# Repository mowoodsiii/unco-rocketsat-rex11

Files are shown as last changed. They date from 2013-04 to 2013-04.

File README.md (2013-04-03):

unco-template
==============
This is the official git repository for the UNCo template project. 

Source (html) for the project's web page is stored in the gh-pages branch of this project. The site is hosted by github, and may be viewed here: [Heliostat Project Page](http://pack3754.github.com/unco-template/index.html)

You may also be interested in the main UNCo Physics Students: Research and Resources pages: [UNCo Physics Students: Research and Resources](http://pack3754.github.com/unco-physics-research)

# project files:
The files are organized into the following structure:
* CMakeLists.txt - cross platform makefiles to make compiling the Heliostat package for any platform (linux, Windows and Mac) easy!
* config - top-level package configuration, including versionn numbers and doxygen configuration files.
* docs - All project documentation will be organized here.
* docs/doxy - Additional doxygen pages to help with source code documentation 
* docs/exported - published (pdf) versions of any important documents
* docs/images - images for use in papers, the web, and documentation
* hw - hardware design documents
* include - distribution header files for the Heliostat C/C++ API

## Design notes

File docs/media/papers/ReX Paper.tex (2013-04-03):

\documentclass{article}
\usepackage{graphicx}
\usepackage{color}
\usepackage{mathptmx}
\usepackage{gensymb}
\usepackage{amsmath}
\usepackage{float}
\usepackage{setspace}
\usepackage[top=1in, bottom=1in, left=1in, right=1in]{geometry}
\usepackage{fancyhdr}
\newcommand{\HRule}{\rule{\linewidth}{0.5mm}}
\setlength{\headheight}{15.2pt}
\pagestyle{fancy}

%\pagestyle{myheadings}
\lhead{\bfseries Reentry Experiment SAT-X}
\chead{\textbf{} U. Northern Colorado}
\rhead{\em \today}

\begin{document}
%%%TITLE PAGE%%%
	\begin{titlepage}
		\begin{center}
			% Upper part of the page
			\textsc{\LARGE Un\underline{iversity of Northern Colora}do}\\[0.7cm]
			\textsc{\Large Colorado Space Grant Symposium}\\[0.7cm]
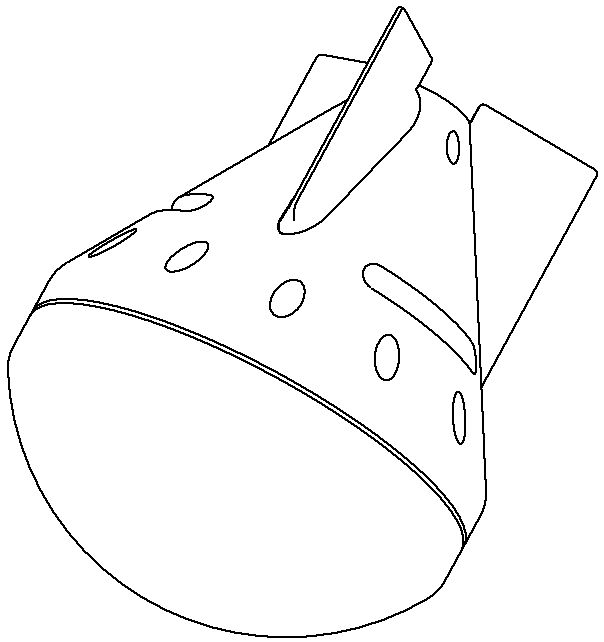
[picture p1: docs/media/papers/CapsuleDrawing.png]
			\\[1cm]
			% Title
			\HRule \\[0.4cm]
			{ \huge \bfseries Reentry Experiment SAT-X:\\} \large Developing an Optimal Atmospheric Reentry Vehicle for the Rocket SAT-X Program\\[0.4cm]
			\HRule \\[1.3cm]
			% Author and supervisor
				\begin{minipage}{0.4\textwidth}
					\begin{flushleft} \large
						\emph{Authors:}\\
						Aaron \textsc{Adamson}\\
						Jordan \textsc{Aken}\\
						Motoaki \textsc{Honda}\\
						Casey \textsc{Kuhns}\\
						Rob \textsc{Shiely}\\
						Maurice \textsc{Woods} (PM)
					\end{flushleft}
				\end{minipage}
				\begin{minipage}{0.4\textwidth}
					\begin{flushright} \large
						\emph{Advisors:} \\
						Cynthia \textsc{Galovich}\\
						Matthew \textsc{Semak}\\
						Robert \textsc{Walch}\\
					\end{flushright}
				\end{minipage}
				\vfill
				\vspace{.75cm}
			% Bottom of the page
				\begin{minipage}{0.4\textwidth}
					\begin{flushleft} 
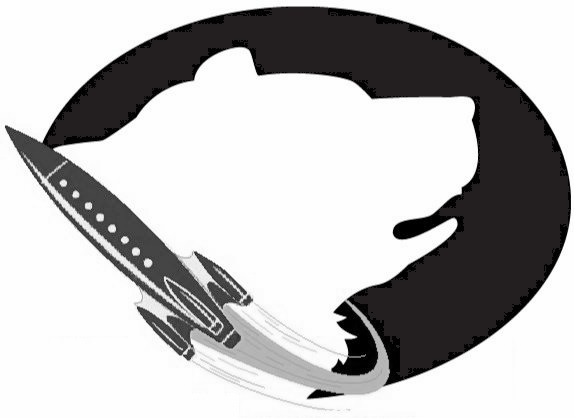
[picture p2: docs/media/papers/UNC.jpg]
						\\
					\end{flushleft}
				\end{minipage}
				\begin{minipage}{0.4\textwidth}
					\begin{flushright}
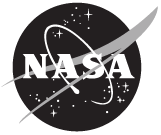
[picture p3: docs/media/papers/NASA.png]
						\\
					\end{flushright}
				\end{minipage}

			{\large \today}\\
			Revision 2
		\end{center}
	\end{titlepage}

%%%BEGIN DOCUMENT%%%
\newpage
%Table of Contents
\tableofcontents	
\newpage

%Abstract
\section{Abstract}
	\begin{doublespace}
	\indent\indent The Reentry Experiment SAT-X (ReX), a joint venture between University of Northern Colorado (UNC) Physics and the Colorado Space Grant Consortium (COSGC), was designed to identify key design aspects associated with atmospheric reentry vehicles and to provide test data that will help to remove dependency on over-engineering as a primary engineering strategy. One of the important considerations for space exploration involves the structural challenges experienced by spacecraft upon returning to Earth. The challenge of entering, or reentering, the Earth's atmosphere is not new, and for years NASA has successfully designed vessels that have endured the harsh process of reentry. However, surprisingly little is actually known about the high atmosphere of Earth. With the insight gained from a simple model of a reentry vehicle's interaction with the atmosphere, a variety of prototypes were tested to determine which design stood the best chance of achieving the ReX mission goals. The ReX payload was launched from Wallops Island at NASA's Wallops Flight Facility in Virginia on 21 July 2011. Funded by the COSGC as part of the Rocket SAT-X undergraduate research program, the payload was flown on an Improved Terrier Orion sounding rocket, and it successfully deployed a small aluminum capsule at apogee (at an altitude of approximately 120 km). The flight was intended to function as a means for characterizing the reentry process and as a proof-of-concept test, showing that the capsule design was an effective platform that could be used for further atmospheric research in the Rocket SAT-X program. The payload design was effective at ejecting a vessel from a spacecraft with few moving parts; it can be constructed in less than a month with less than a \$3000 budget, and it is easily modifiable to accommodate new mission hardware (ideal for the Rocket SAT-X program). We are currently revising the ReX design in an attempt to improve the payload's radio telemetry connection, thus increasing the amount of data recovered from the flight and improving the resolution and dependability of the payload's instruments.
	\end{doublespace}

%Introduction
\section{Introduction}
	\begin{doublespace}
		\indent\indent The challenge of entering, or reentering, the Earth's atmosphere is not new. For years, NASA has successfully designed vessels that have endured the harsh process of reentry. However, in some cases, this was made possible through the act of over-engineering; designing to withstand conditions far beyond what is expected to be encountered. Though this method has proven effective, consider the benefit of knowing exactly what to expect. The objective of the University of Northern Colorado Reentry Experiment SAT-X (UNC ReX) was to shed light on the process of atmospheric reentry and provide test data that will help to remove our dependency on over-engineering. Moreover, as a secondary objective, the capsule's design was evaluated to determine its effectiveness in serving as a platform for use in future Rocket SAT-X missions. This evaluation took into account the resources and skills needed to produce the capsule.\\
		\indent This mission was carried out as a part of UNC Physics' involvement with ``Rocket SAT-X", an outreach program funded by the Colorado Space Grant Consortium (COSGC) that presents undergraduate students with an opportunity to become involved in aerospace engineering and the aerospace community at an advanced level. The Rocket SAT-X program challenges students to design and fabricate an experimental payload that will be launched on a Terrier-Orion sounding rocket, provided and launched by NASA's Wallops Flight Facility in Virginia. Four university-made payloads were launched approximately 120km into space, where the rocket then shed its fairing, exposing the payloads to the space environment (Figure~\ref{timeline}). \\
		\indent In an effort to document the methods used throughout this project, this report will discuss both the physics and the engineering behind the reentry experiment for future reentry Rocket SAT-X missions.
	%Mission Statement and Background
	\subsection{Mission Statement and Background}
	\begin{center}
		\emph{To provide a robust design of a deployable and recoverable payload for institutions to use on future Rocket SAT-X missions. With the provision of local data storage, we can greatly increase the amount of data recovered by eliminating the need to transmit restricted amounts of data to the ground.}\\
	\end{center}
		\indent\indent  By collecting extensive dynamical and thermal data as the reentry vehicle enters the earth's atmosphere, ReX aims to provide information on the reentry process of a particular type of vehicle. After reviewing the flight data and comparing it to a mathematical model (outlined in the Methods section) the design of the capsule will be reviewed for its effectiveness as a reentry vehicle. Moreover, this data will be used in refining the model to aid in optimizing the payload design. This analysis will be conducted to the extent that any future Rocket SAT-X team using this capsule platform will be able to predict the details of the capsule's motion (its trajectory and motion about its center of mass), what temperatures will be experienced during flight, and what the general limitations of the capsule platform will be at any given time during a mission.
	%Success Criteria
	\subsection{Success Criteria}
		\indent\indent In order to achieve full `missions success', the ReX payload was required to collect enough usable data at a high enough resolution to create a reliable flight characterization profile for the ReX reentry vehicle. Additionally, this had to be achieved while optimizing the vehicle's mass, size and technological complexity -- a secondary objective to the ReX mission. The resolution needed to create such a profile is determined by the ability of the onboard sensors to detect both large and small deviations in the vehicle's flight path, such as oscillations, high-G accelerations, and turbulence. Also, since extreme heat is characteristic of the reentry process, sensors were required to measure where heat builds up on the vehicle surface. Finally, the payload was designed to survive long enough to allow  data collection until impact (splashdown).\\
		\indent ``Full mission success" would only have been claimed if all of these objectives were met. However, considering the possibility that some objectives may not be met for any reason, levels of ``partial mission success" could be achieved if some of the more basic functions of the payload worked correctly despite the failure of other functions (e.g. if the capsule is ejected but data were not transmitted back to the rocket, then the mission would be considered a ``partial mission objective success").\\
		\indent It is important to note that the mission supervisors at Wallops Flight Facility and the COSGC instated a number of mission requirements beyond those set by the ReX team. Given that the ReX payload involved the ejection of a reentry vehicle that was designed to remain intact throughout descent and splashdown, concern was raised about the possibility of the payload landing in a populated area, presenting a potential hazard to those civilians who may be near a debris fallout area. NASA requires that spacecraft reentry must not exceed a 1:10,000 probability of exposing the ground population to risk (Rochelle, 2004). Therefore, the team was required to ensure that the reentry vehicle would be ejected in a manner that would minimize the risk of becoming a hazard to the ground population. An ejection velocity of no more than $5\frac{m}{s}$ was predicted to keep the capsule within a safe impact radius.
		\end{doublespace}
		
%Methods
\section{Methods}
	\begin{doublespace}
	\indent\indent In an effort to better understand the conditions that would be experienced during the reentry process, the ReX team first studied the fundamental physics of the expected descent. Using a mathematical model, the team optimized the payload's design by building the capsule to specifications that were calculated to enable the capsule to survive the descent from apogee and impact with the ocean.
	%Physics of Reentry
	\subsection{Physics of Reentry}
	\indent\indent Using MATLAB (a technical computing environment), Motoaki Honda developed several programs for use in modeling the flight of the capsule. The programs were to serve three purposes: 1) predict the force of impact that the capsule experiences upon splashdown, 2) predict the amount of energy due to air friction that is imparted to the capsule during its descent (calculate the heat of reentry), and 3) provide a graphical user interface testing tool for visualizing the instantaneous orientation of the capsule during drop tests (also used to ``monitor" the motion of the capsule during flight). The following subsections are an overview of some of the basic concepts that were used in the mathematical model.
		%Forces
		\subsubsection{Forces}
		\indent\indent To model the process of atmospheric reentry, it is important to know what forces are being exerted on the reentry vehicle. Taking a purely Newtonian approach, the most prominent force  associated with reentry is air resistance (Pardini and Anselmo, 2004). This is expressed by
		\begin{equation}
			F_{air drag}=\frac{1}{2}\rho(h) v^{2}AC_{d},
		\end{equation}
		where $\rho$(h) is air density as a function of the altitude, h, above the surface of the earth, $v$ is the capsule's speed, A is the capsule's cross-sectional area, $C_{d}$ is the drag coefficient associated with the capsule's geometry. So, taking this and the force of gravity into account, the capsule's resultant vertical acceleration is given by\\
		\begin{equation}
			a_{resultant}=g(h)-\frac{\rho(h)v^{2}AC_{d}}{2m},
		\end{equation}
		 where g(h) is the altitude-dependent acceleration rate due to gravity and m is the mass of the capsule. Next, recall that g(h) is given by Newton's law of universal gravitation,
 		\begin{equation}
			g(h)=\frac{GM_{earth}}{(R_{earth}+h)^{2}}		
		\end{equation}
		where G is the universal gravitational constant, $M_{earth}$  is the mass of the earth, and $R_{earth}$ is the radius of the earth. With these relations, one can develop the capsule's altitude-dependent speed profile. This is important in what is to come.
		%Air Density
		\subsubsection{Air Density}
		\indent\indent The atmosphere of the earth is not easily describable as there are a great number of variables that cause variations in its composition. As a result, there is no general equation for the density of air with respect to altitude. However, there is information available that describes the atmosphere as a set of layers, each characterized by an average density (Haynes, 2012). Using this data and interpolating with the assumption that the density decays exponentially over each layer, a continuous density profile can be developed by `stitching together' the estimated density profile for each layer (Figure \ref{stitch}).
 		%The 'Atmospheric Wall'
		\subsubsection{The ``Atmospheric Wall"}
		\indent\indent As the ReX capsule descends from space, there is a period of time during which the capsule will effectively be in free fall as drag is negligible. This occurs when the capsule is outside of the earth's atmosphere, which begins at an altitude of roughly 50km (Haynes, 2012). At this altitude, the capsule will experience a sudden increase in atmospheric density. This marks the boundary between a region of virtually infinite terminal velocity to one of significantly lower terminal velocity. Given that that the capsule will have accelerated to a relatively large speed within the free fall region, it will experience a significant deceleration as it crosses this boundary. This sudden deceleration was referred to as ``hitting the atmospheric wall", since the capsule's encounter with the atmosphere is analogous to hitting a wall of air. As the object is dropped from increasingly larger heights, the impact from hitting this `wall' becomes greater (Figure \ref{accel}).
		%Work Done by Air Friction
		\subsubsection{Work Done by Air Friction}
		\indent\indent The capsule's sudden deceleration caused by encountering the `atmospheric wall' can induce not only a large amount of G-shock to the body of the capsule, but also significant heat buildup due to air friction. This became a topic of concern in the design of the payload as both effects could prove hazardous to the functionality of the capsule. In order to estimate the amount of energy involved in heating the capsule, the energy generated by the drag was considered. Using the model for the drag force and the velocity of the capsule throughout its descent (outlined in Section 3.1.1), the magnitude of the power generated due to air drag, $|P|=F_{air drag}v$, was calculated as a function of time. Finally, the power profile was integrated over time to reveal the total energy lost due to drag. This value served as an estimate of the upper bound on the energy that went into heating the capsule (as there was an uncertainty as to how much of this energy was transfered to the atmosphere rather than the capsule) (Figure \ref{heat}).\\
		\indent The mathematical model estimated that more than 2MJ of energy would go into heating the capsule, which would threaten to melt the capsule's aluminum body if the amount of aluminum used to make the capsule was too little. This information led to a side effort to design an ablative heat shield that could be placed over the front of the payload to reduce the amount of thermal energy transfered to the capsule. While this effort was not incorporated into final capsule design, more about the heat shield is included in the ``Payload Design" subsection.\\
		\indent The mathematical model also considered other mechanisms for heat transfer between the capsule and the air. This took into consideration the fact that the air around the capsule would be heated by the capsule itself and what effect this might have on the transfer of energy. Additionally, in the absence of the proper resources to conduct such a test, heating profiles of similarly-shaped spacecraft from other published works were reviewed in order to understand the importance of orienting the reentry vehicle with a stable trajectory so as to prevent imbalances in the heating of the capsule (Pezzella and Viviani, 2011). 

	%Payload Design
	\subsection{Payload Design}
		\indent\indent Based on the mathematical model, there are two aspects of the reentry process that govern the design of the reentry vehicle: thermal loading and sudden changes in velocity (particularly upon landing). By reducing the drag profile of the capsule, the thermal loading on the skin of the vehicle can be significantly reduced. However, by doing this, the resistance to moving through the air is also reduced causing the terminal velocity of the capsule to increase to a level that may cause structural failure upon landing. On the other hand, increasing the drag profile of the capsule reduces the terminal and impact velocities of the falling reentry vehicle but could cause the capsule to overheat due to friction with the atmosphere. Therefore, an appropriate balance between the two hazards must be found.\\
		\indent The ReX team created several prototypes (Figure \ref{proto}) that were used to test the various aspects of flight. While the mathematical model could be used to determine a theoretical value for the terminal velocity and thermal loading for each prototype, additional short range drop tests were also necessary to determine which capsule design was best at orientating itself into a proper, straight-down trajectory (ideally, the capsule would fall nose first without tumbling or high-speed spinning which could cause damage to the internal electronics).  Research involving the development of reentry vehicles by NASA and Boeing suggested that one of the most effective reentry vehicles was the Apollo capsule, used in the 1960's and 70's at the dawn of manned spaceflight (Sietzen, 2011). The Apollo shape features a wide convex disk at its base which created a large drag profile that was structurally supported by the conical shape that was positioned on top of the disk. While this design was promising at first, the team realized that the Apollo capsule was not a freely falling object but was oriented with the help of thrust rockets that could be fired in any direction to maintain a stability about the thrust axis (Cole, 2008). After performing several drop tests, the ``stream-line shaped" capsule (which still retained many of the Apollo spacecraft's basic design features) was deemed to be the most suitable candidate for the final payload design, as the incorporation of tail fins compensated for the lack of rocket-based flight stabilization. Not only did the design orient itself flawlessly during each drop test, but the mathematical model seemed to support the possibility of such a shape surviving the strongest impact of the four designs.\\
		\indent The team then focused on creating a heat shield for the nose of the capsule to prevent overheating and meltdown due to air friction. Due to the intense vibrations and accelerations of launch, ceramics and the more traditionally rigid types of heat shields were deemed inadequate. Instead, the team tested several combinations of carbon fiber and graphite-based epoxies to protect the capsule from the intense heat. A layer of carbon fiber weave, glued on with an epoxy infused with graphite powder, was the most effective means of protecting the capsule (Figure \ref{shield}). However, due to time constraints and difficulties with developing a reliable method for attaching the heat shield to the nose of the capsule, the heat shield was not included in the final payload design.
	%Sub-Systems Overview
	\subsection{Sub-System Overview}
		%Hardware
		\subsubsection{Hardware}
		\indent\indent The ReX payload consisted of one ejectable reentry vehicle that housed an assortment of sensors used to gather dynamical and thermal data during reentry. In addition to the reentry vehicle, the payload was outfitted with a reentry capsule launcher used to jettison the capsule from the rocket body after fairing deployment at rocket apogee.\\
		\indent The exterior housing of the reentry vehicle was designed as a mixture of two `ideal' reentry shapes. As discussed in Section 3.2, the Apollo capsule was chosen as a model for the ReX reentry vehicle. The Apollo capsule's shape provides a great deal of interior space for housing electronics, presents a large, forward-facing surface for heat dissipation, and a low center of gravity that aids in stabilizing the capsule during flight. Additionally, the smooth, conical shape is easily machined, allowing the team to fabricate multiple versions of the same payload for prototyping and testing. However, the Apollo-shape profile alone is not sufficient, as the prototype failed to properly orient itself in a downward-facing `flight trajectory' during testing. To correct for this, the design was modified to incorporate a profile that was more streamlined. With the addition of tail fins to an elongated aft section, the hybrid streamlined-Apollo capsule (Figures \ref{proto} \& \ref{capsule}) exhibited exceptional self-orienting characteristics that will allow the capsule to travel through the earth's atmosphere with minimal tumbling and heating.\\
		\indent  In order to prepare the capsule for a reentry flight, it must be released from the sounding rocket body after the fairing of the rocket has been deployed (Figure \ref{ejection}). To ensure that the capsule is clear of the rocket as it is released, a small spring pushed the capsule from the rocket at approximately $1\frac{m}{s}$ (knowing the expected rotation rate of the rocket, this was the speed required to avoid collisions with any objects protruding from the spinning rocket body). This spring was compressed and placed at the tail of the capsule, which was held in place by a locking mechanism incorporated into the capsule launcher harness. However, to ensure that ejection of the capsule would not occur prematurely, a cylindrical locking cam was designed to lock the capsule in place during launch using positive pressure to ensure that the lock was still engaged regardless of power supply or control systems status (Figure \ref{harness}). When apogee was reached, the motor rotated the cam causing the locks to disengage and release the capsule.\\
		\indent The payload was equipped with multiple microcontrollers, each responsible for collecting data and controlling certain events that must be initiated during the flight. To do this, two main electrical systems were designed, one on the base station and one on the reentry vehicle. Both systems were derived from the ATmega2560 microcontroller and incorporated an array of sensors to completely characterize the three-dimensional motion of the individual components throughout the flight. The sensor equipment included an HMC5843 triple-axis magnetometer, two ADXL345 triple-axis accelerometers, an ITG3200 triple-axis gyroscope, and a LPR530AL dual-axis and LY530AL single-axis gyroscope, all bought from SparkFun Electronics. Additionally, the capsule was designed to carry several temperature sensors to collect data concerning the thermal loads and thermal gradient experienced on the skin of the capsule at different points during the reentry process. However, due to complications with adhering the sensors to the aluminum shell, these temperature sensors were not included in the finished payload.\\
		\indent The base station and capsules communicated via 900MHz radio transceivers. Because these radios were housed within the capsule's aluminum shell, an antenna was necessary to allow the transmission of radio signals to and from the reentry vehicle. To accommodate for this, the tail fins on the tail of the capsule were constructed from printed circuit-board (PCB) that contained a copper trace that would act as an antenna situated outside of the capsule (Figure \ref{antenna}). The antenna's length and shape was designed with the help of First RF in Boulder, CO, who helped the ReX team optimize that antenna's effectiveness.\\
		\indent The base station had several unique functions. It was primarily responsible for receiving and interpreting several timing events from the rocket telemetry. That information was used to activate the subsystems aboard the payload, including a shock resistant, high definition video camera, reentry vehicle electronics, and the launching/capsule release mechanism. The base station also transmitted real-time data and status updates to the launch facility via a telemetry link to the ground, provided by Wallops (Figure \ref{FBD}). The final layout of the ReX payload is pictured in Figure \ref{layout}
		%Software
		\subsubsection{Software} 
		\indent\indent Since the flight included a wide range of acceleration and roll rates that were to be recorded, the gyroscopes and accelerometers operated at different ranges (eg. high/low-G) in order to properly cover the spectrum to be measured. If the high detail, limited range sensors saturated at any point of data collection, the software reverted to the high range sensors, so that neither range nor accuracy would have to be sacrificed. All of the data generated by the sensors was stored locally on non-volatile flash memory cards. The reentry vehicle computer sent an abbreviated, lower resolution copy of the flight data to the base station via 900MHz XBee (DigiKey) radios at 115200 baud. For real-time monitoring (and in case of an unrecoverable payload), the maximum amount of data allowed through the 900MHz connection was transmitted using the rocket's telemetry link to the launch facility.\\
		\indent The base station utilized a series of telemetry and power connections controlled by Wallops Flight Facility to receive timing events from, and transmit data to, the launch facility. The first timing event occurred at T+8 seconds, at which time the base station powered on, ran through the self-diagnostics procedure and initiated a full resolution recording of acceleration and roll rates for the duration of the mission. The last timing event occurred when the fairing was removed from the rocket, to indicate readiness for capsule ejection. 
To transmit data, there were ten parallel lines, each of which was used to indicate the payload's status during the flight. There were also four analog lines utilized by the base station that measured the signal strength of the capsule radio connection. Finally, a single serial connection running at 19200 baud provided summarized segments of the dynamical data transmitted by the capsule throughout the flight. 
	\end{doublespace}
						%%%%Capsule Return Reward%%%%%
						%%%%%Payload Layout (Final Assembly)%%%%	
	%Testing
		%Radio and Sensor Tests
		%Tall Tower
	%Launch and Integration
						%%%%PAYLOAD STACK%%%%

%Results
\section{Results}
	\begin{doublespace}
	%Hardware Survival 
	\subsection{Hardware Survival}
		\indent\indent Recovery of the ReX payload after mission termination and splashdown suggested that the capsule was ejected properly at apogee. Successful ejection was confirmed by viewing the onboard video footage of the rocket body and its payloads (Ogg \& Goh, 2011). This showed the capsule leaving the rocket roughly eight seconds after fairing separation, drifting away at a reasonable speed with a nominally stable trajectory. The capsule did not appear to tumble at this time and was oriented so that the nose cone faced the earth (in the direction of descent). The reentry capsule body has  not been recovered. Physical examination of the recovered rocket payload section showed that the payload's computer and electronics box was missing altogether. Evidence of scrapes and buffs in the aluminum deck plate and on the aluminum container of the University of Wyoming's AstroX payload (located directly beneath the ReX payload) suggests that the four M6 bolts that fastened the electronics containment box to the deck plate had been ripped out, allowing the box to detach itself from the rocket. Additionally, the cables that connected the various electronics on the deck plate had been completely severed, not only by the apparent pull of the electronics box as it detached from the rocket, but also from the evidence that the payload underwent so much thermal loading that the rosin-core solder had completely evaporated away. The solder bonded the payload's electrical connections to their respective terminals and the melting of the solder left no bonding agent to connect the wires to the electronics (rosin-core solder has a melting point of about 350\degree C). The evidence of thermal loading was also apparent from the discovery of char marks that streaked across the payload. The heat of reentry, being enough to vaporize solder, burned the plastic off of the Kevlar belt that was used to rotate the locking mechanism of the capsule launcher depositing streaks of black residue on the payload.\\
		\indent The on-board, high-definition video camera and the enclosure in which it was housed (mounted to the deck plate) survived reentry with no adverse effects. However, the SD memory card inside the camera was not functional. Upon inspection, the memory card was corrupted. After dissembling the card, the electrical contacts were throughly cleaned to minimize the damage possibly caused by exposure to seawater. A data recovery program was then utilized to try and obtain any information that may have been stored on the card. This effort proved fruitless, and the only video of the reentry vehicle ejection was provided by CU.
	%Effectiveness of Sensors
	\subsection{Effectiveness of Sensors}
		\indent\indent Telemetry data collected and recorded by Wallops Flight Facility suggested that the ReX payload failed to collect any useful dynamical data from any of the capsule's sensors. The telemetry log showed that the payload's umbilical to the capsule (designed to connect the capsule electronics to the rocket electronics) was operational until capsule separation. After ejection, the capsule's sensors were functional for only six seconds, after which time only intermittent signals were received (Figure \ref{raw}).
		\end{doublespace}

%Discussion
\section{Discussion}
	\begin{doublespace}
		\indent\indent The results of the ReX flight data, both through physical evidence and through interpretation of the data, suggest that the mission was only a partial success. The primary mission objective, to successfully deploy a self-contained capsule from the rocket body, was achieved. The capsule release mechanism opened without incident, the ejection spring accelerated the capsule from the rocket to an optimal speed, no collisions occurred between the ejected capsule and the rocket (i.e., there was no evidence of a ``tip off" -- when the tail fins of the capsule are struck by the rocket, causing the capsule to tumble), and video footage of the ejection was acquired for the entire time that the capsule was visible. However, for all practical purposes, the mission did not yield any quantifiable data from the sensors housed on the rocket nor within the reentry capsule. This was due to the fact that there was a fatal error that occurred with the radio connection between the capsule and the rocket payload, as the telemetry data recorded less than ten seconds of data. Any data that were collected during the flight and recorded on the SD card housed within the electronics containment box was lost when the electronics box was ripped off of the deck plate -- no ``hard data" were collected from the flight. However, it is worth mentioning that the char marks on the deck plate left an outline around what was once the electronics containment box. This suggests that the ejection of the electronics box occurred well after the capsule's deployment, therefore ruling out the theory that the lost data connection indicated on the telemetry log was due to a physical failure. Instead, it was due to an error within the electronics/radio system. Unfortunately, without the electronics containment box and without sufficient telemetry data, the ReX team has been unable to diagnose the issues of the flight any further. However, lessons can be learned from the study of the hardware that was recovered from the flight.
	\end{doublespace}

%Conclusions
\section{Conclusions}
	\begin{doublespace}
		\indent\indent The ReX mission was considered a ``partial mission success", based on the \emph{Success Criteria}. While the electronics of the payload failed for unknown reasons, the mechanical system successfully deployed the reentry capsule from the rocket. Even so, it is obvious that the ReX payload contained several design flaws that are now understood from the de-integration of the payload post-flight. Future missions will require the use of RTV (Room-temperature vulcanization), a non-conductive, silicone-based rubber that is used to insulate solder joints from extreme heat and corrosion. Using RTV may have prevented the vaporization of the solder joints that connected the payload's wires to the various electrical components within the electronics containment box, potentially extending the lifetime of the data-collection systems. Furthermore, the absence of the electronics containment box post-flight suggested that the hardware that was used to restrain the box was insufficient or faulty. The helicoils (threaded inserts used to give holes drilled in soft metals a threaded finish, allowing for the use of bolts and screws) that held the M6 bolts to the deck plate had been ripped out. This may be prevented in the future by using more than four bolts to restrain mechanisms to the deck plate.\\
		\indent Of course, the true limiting factor in the design and manufacturing processes of the ReX mission was time. While the team put many hours into constructing the payload, the mission goals were more ambitious than initially anticipated. However, it is reasonable to consider the 2011 Rosanova 41.029 flight as a first trial for an ambitious project to be improved and expanded.
	\end{doublespace}
	%Future Refinement (RAPTR SAT-X)
%	\emph{Future Missions (RAPTR SAT-X)}\\
%		\indent RAPTR
	%Contributions to NASA
	\subsection{Contributions to NASA}
	\begin{doublespace}
		\indent\indent The secondary objective of this project was to utilize the ReX team's unique skill set and hardware access to be able to design a generic platform that COSGC would be able to offer to other schools that may not have the resources of the ReX team. By developing a tested platform to carry and eject payloads into space, future deployable-based university payloads would be able to spend more time on the science of the project, rather than spending time developing the vehicle used to carry and eject it. The ReX capsule, complete with design diagrams and relatively simple manufacturing, makes the possibility of space experiments much less intimidating when a major portion of the engineering has already been completed and tested.  This objective was achieved as the launch mechanism functioned properly, and the capsule was safely ejected and reentered the atmosphere.
	\end{doublespace}

\newpage
%Acknowledgments
\section{Acknowledgments}
	\begin{doublespace}
		\indent\indent The five members of the Reentry Experiment SAT-X team spent a full year designing, testing, perfecting, launching, and analyzing the small piece of aluminum that would be each member's "first item in space". While each member devoted ample amounts of time to see the ReX mission to its completion, ReX would not have been as successful as it was had it not been for the many people that helped along the way. Special thanks is due to Dr. Cynthia Galovich, Dr. Matthew Semak, and Dr. Robert Walch (physics professors at the University of Northern Colorado), and Ken Cochran and Chad Wangeline (technical staff members at UNC) for their advice and support. Also, two companies, Road Narrows Robotics of Loveland, CO and First RF of Boulder, CO, were instrumental in providing workspace and radio-engineering advice. Finally, the advising bodies at the Colorado Space Grant Consortium (particularly mission manager, Shawn Carroll) and NASA's Wallops Flight Facility were extremely helpful and were an invaluable resource to the ReX team.\\
		\indent A web-page containing pictures and videos of the ReX project is located at the following URL:\\ \textcolor{blue}{http://www.facebook.com/pages/University-of-Northern-Colorado-Rocket-SAT/162201893803346}.\\ The ReX team invites you to review the page to keep up with future UNC rocket missions.
	\end{doublespace}

%Literature Cited
\section{Literature Cited}
	\begin{doublespace}
Cole, E. G. (2008). DESIGN AND DEVELOPMENT OF THE APOLLO THREE-MAN SPACECRAFT WITH\\
\indent TWO-MAN LUNAR EXCURSION MODULE (LEM). Annals of the New York Academy of Sciences, 134(1),\\
\indent 39-57. doi:10.1111/j.1749-6632.1965.tb56141.x\\
Ogg, C. (Designer), \& Goh, A. (Designer) (2011). Rosanova 41.092 onboard payload survalence [DVD].\\
Pardini, C., \& Anselmo, L. (2004). On the accuracy of satellite reentry predictions. Advances in Space Research,\\ \indent 34(5), 1038-1043. doi:10.1016/j.asr.2003.01.010\\
Pezzella, G., \& Viviani, A. (2011). Aerodynamic analysis of a mars exploration manned capsule. Acta\\
\indent Astronautica, 69(11), 975-986. doi:10.1016/j.actaastro.2011.06.020\\
Rochelle, W. C., Marichalar, J. J., \& Johnson, N. L. (2004). Analysis of reentry survivability of UARS spacecraft.\\ \indent Advances in Space Research, 34(5), 1049-1054. doi:10.1016/j.asr.2003.01.011\\
Sietzen Jr. (2011). Son of apollo: A new space capsule takes shape. Aerospace America, 49(1), 36.\\
Sim, H., \& Kim, K. (2011). Reentry survival analysis of tumbling metallic hollow cylinder. Advances in Space\\ 
\indent Research, 48(5), 914-922. doi:10.1016/j.asr.2011.04.036\\
U.s. standard atmosphere. In (2012). W. Haynes (Ed.), \emph{CRC Handbook of Chemistry and Physics} (pp. 555-999).\\ \indent Retrieved from http://www.hbcpnetbase.com/

	\end{doublespace}
	
%Figures
\newpage
\section{Figures}
	\begin{figure}[h]
	\begin{center}
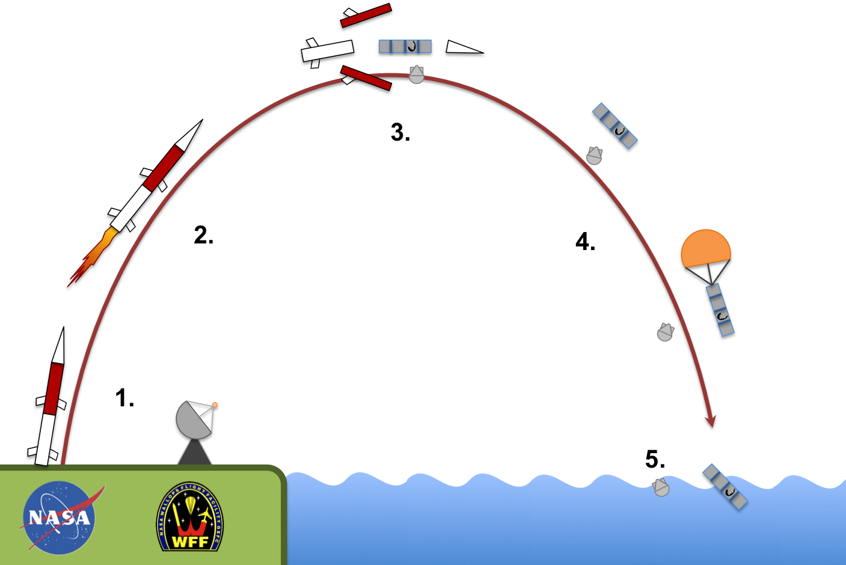
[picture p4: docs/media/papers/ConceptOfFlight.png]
		\\
	\end{center}
		\caption{}
		\label{timeline}
Concept of flight timeline\\1. Launch,  2. Ascent; Onboard electronics initialize,  3. Apogee; Fairing deployment, ReX capsules ejected,  4. Descent; ReX Capsules collect data, data transferred via XBee radio to rocket then to ground via Wallops telemetry connection,  5. Splashdown.
	\end{figure}

	\begin{figure}[H]
	\begin{center}
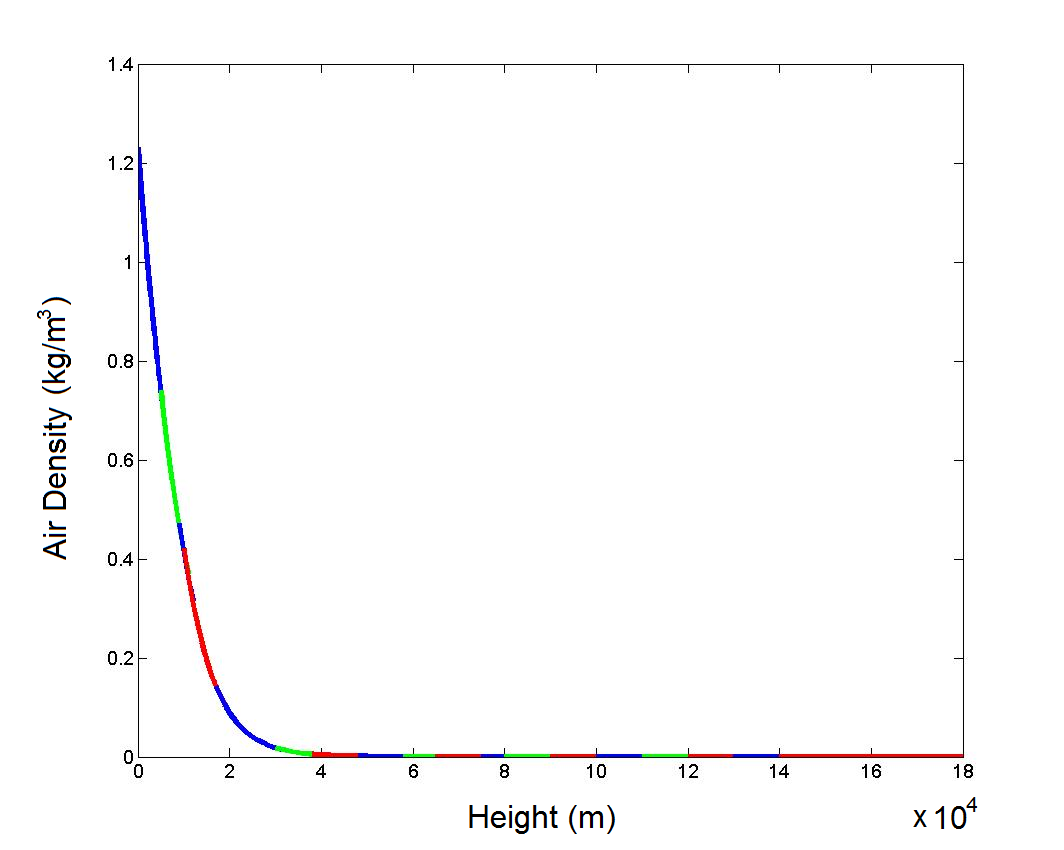
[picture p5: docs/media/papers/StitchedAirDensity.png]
		\\
	\end{center}
		\caption{}
		\label{stitch} 
The continuous atmospheric density profile\\ This profile was constructed by stitching together the estimated density profile for each layer of the atmosphere for use in the mathematical model (Haynes, 2012). Each color represents a layer of the atmosphere for which the density profile was estimated.
	\end{figure}
	
\newpage
	\begin{figure}[H]
	\begin{center}
		(A.)
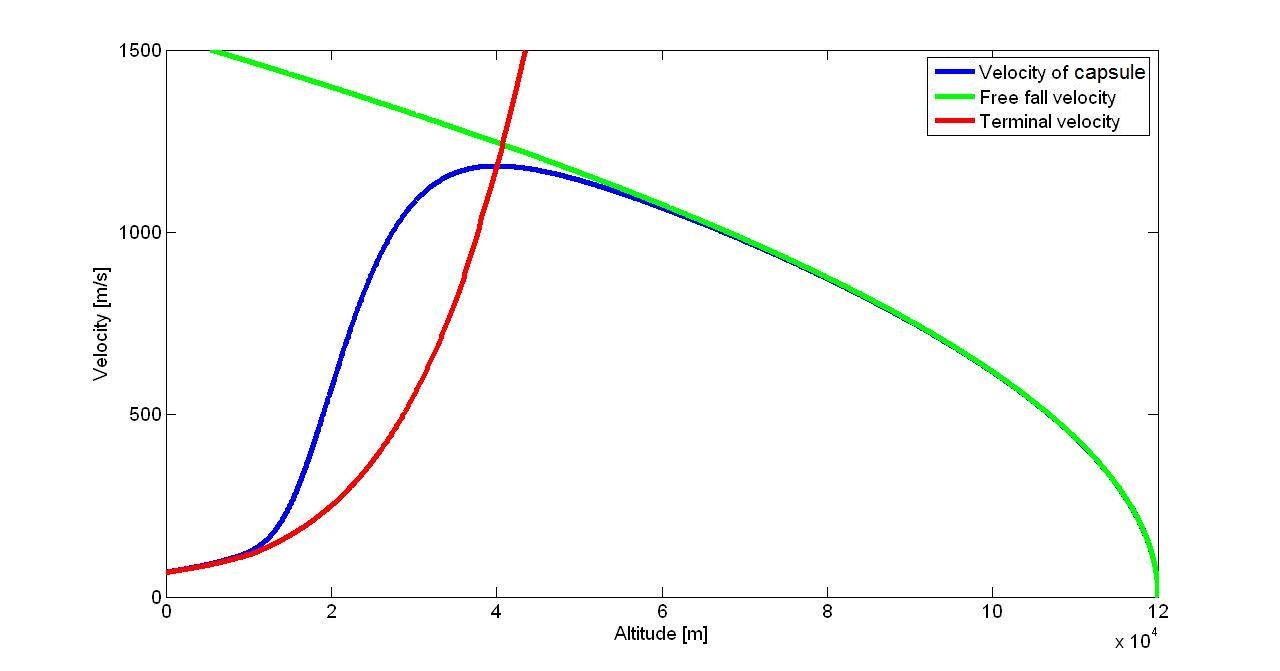
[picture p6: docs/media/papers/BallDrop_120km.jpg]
		\\
		\vspace{1cm}
		(B.)
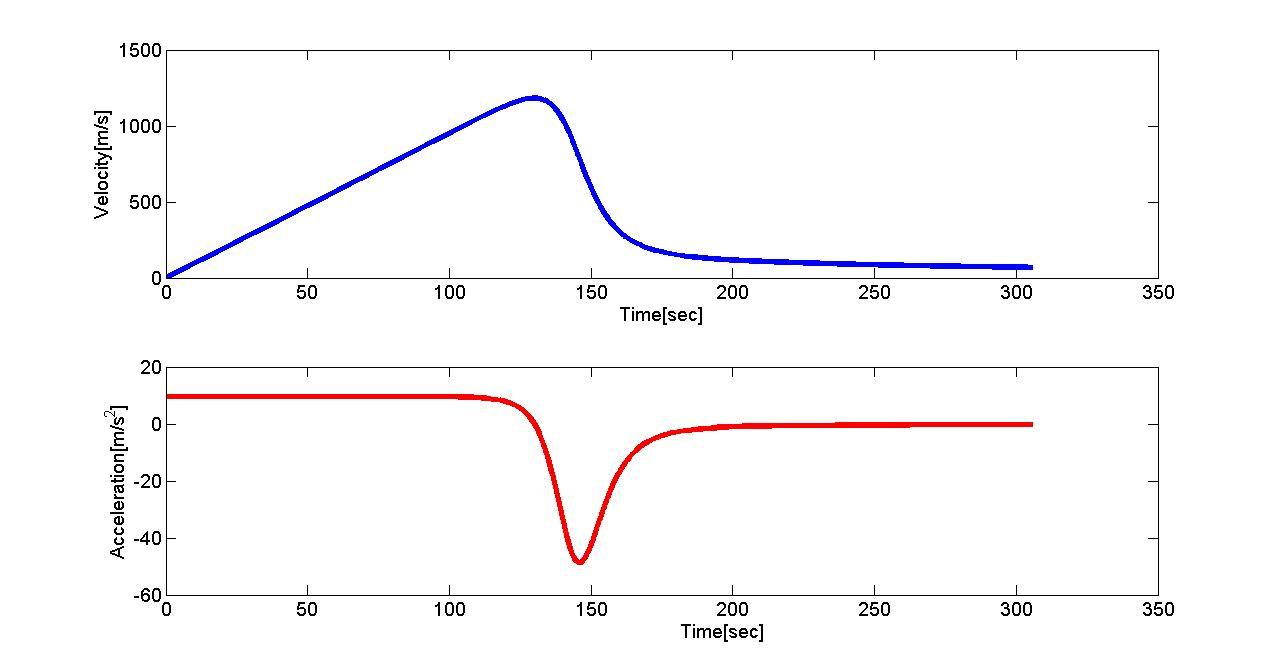
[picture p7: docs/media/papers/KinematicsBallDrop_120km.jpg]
		\\
	\end{center}
		\caption{}
		\label{accel}
Expected velocity and acceleration profiles of the capsule during reentry\\ (A) This velocity profile shows the point at which the capsule is expected to deviate from a free fall trajectory to one with considerable drag. The green curve represents a purely free fall scenario, whereas the blue curve is the expected trajectory that includes the effects of both gravity and air resistance. The red curve is the terminal velocity corresponding to the motion profile of the blue curve. Notice: Where the green and blue curves coincide is the range of altitudes over which the capsule is freely falling, where as the point at which the blue and green curves deviate is the altitude at which the capsule encounters a sudden increase in atmospheric density (ie. ``hits the atmospheric wall"). As seen by examining the red curve, the capsule's speed is higher than its expected terminal velocity for a considerable portion of the flight though the higher-density region.\\ (B) This specific velocity/acceleration profile shows the large negative acceleration experienced in hitting the atmospheric wall.
	\end{figure}

\newpage
	\begin{figure}[H]
	\begin{center}
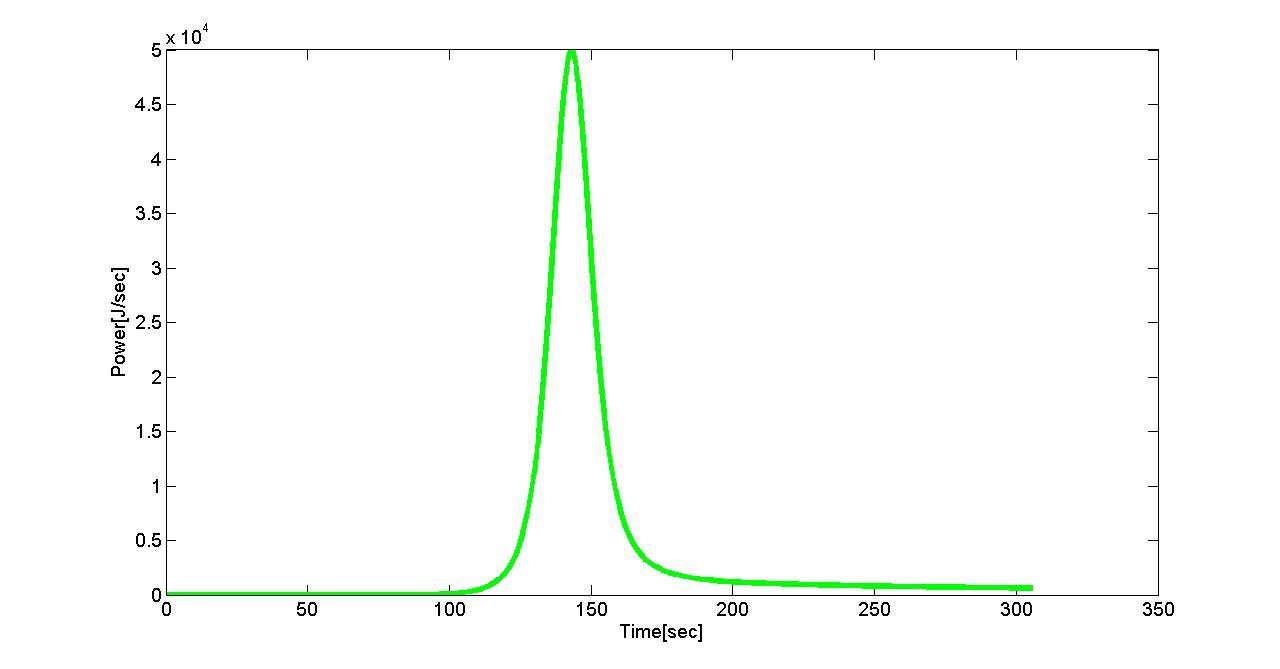
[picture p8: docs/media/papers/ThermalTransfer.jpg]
		\\
	\end{center}
		\caption{}
		\label{heat}
Thermal energy of reentry\\ \indent This is the power generated due to the drag force opposing the capsule's motion through the denser regions of the atmopshere. The area beneath the curve corresponds to the total work done by air friction, which will be transferred into heating up the surface of the reentry object.
	\end{figure}

	\begin{figure}[H]
	\begin{center}
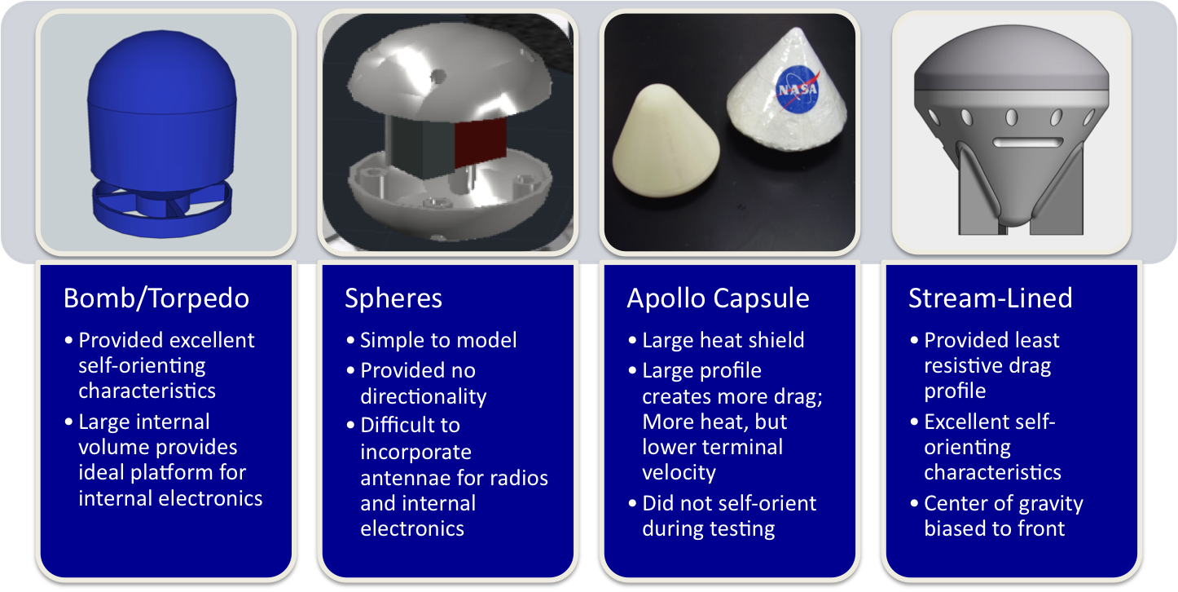
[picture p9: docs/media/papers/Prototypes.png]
		\\
	\end{center}
		\caption{}
		\label{proto}
Capsule prototypes\\ Four prototype concepts for the ejectable reentry capsule. The stream-lined shape (an elongated version of the Apollo capsule with tail fins) was decided to be the most appropriate shape for the final reentry vehicle.
	\end{figure}

\newpage
	\begin{figure}[H]
	\begin{center}
		(A.)
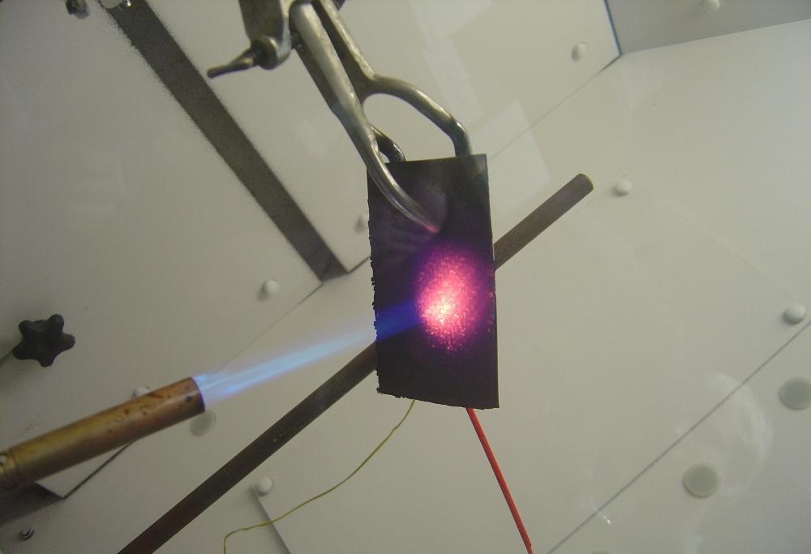
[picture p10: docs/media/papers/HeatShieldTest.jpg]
		\\
		\vspace{1cm}
		(B.)
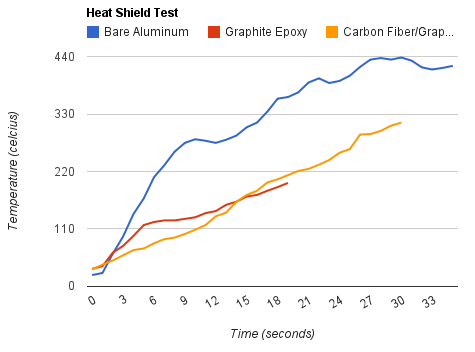
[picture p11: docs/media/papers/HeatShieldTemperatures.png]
		\\
	\end{center}
		\caption{}
		\label{shield}
Heat shield development\\(A) An image of the heat shield testing setup: sheets of aluminum were suspended over a butane torch flame for several seconds. Temperature probes were attached to the back of each sheet while the aluminum was heated which recorded the temperature of the back-side of the aluminum every five seconds. \\(B) Average temperature data from three trials of three heat shield types: Bare Aluminum (control/no heat shield), graphite epoxy (an epoxy paste mixed with graphite powder that was smeared over the face of the aluminum and allowed to dry), and carbon fiber weave that was glued to the aluminum using the graphite epoxy paste. Trials were conducted until a relative equilibrium was reached or until a catastrophic failure of the aluminum occurred. 
	\end{figure}

\newpage
	\begin{figure}[H]
	\begin{center}
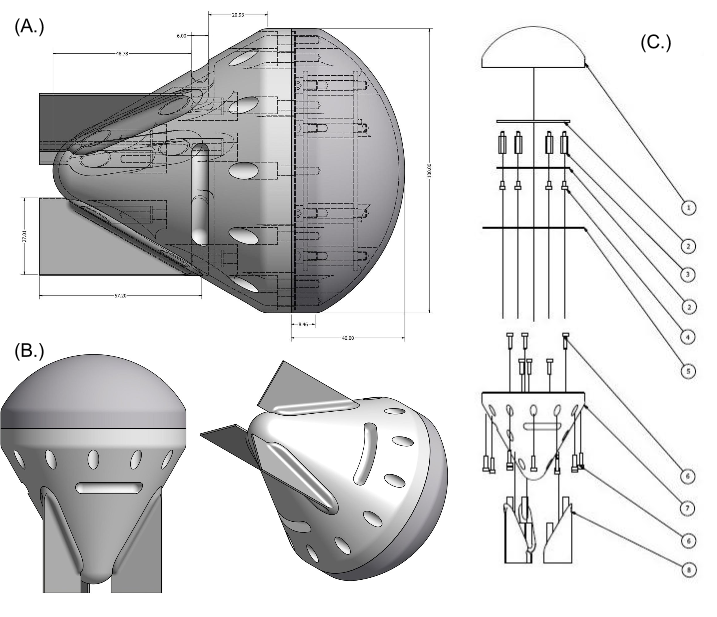
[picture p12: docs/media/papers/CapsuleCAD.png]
		\\
	\end{center}
		\caption{}
		\label{capsule}
Digital model of reentry capsule\\ (A) Cross-sectioned dimensional view. \\(B) Side and isometric view. \\(C) Exploded view with labeled components: 1. Nose Cone, 2. Electronics deck, 3. Standoff, 4. Nose bolt, 5. Junction Gasket, 6. Junction bolt, 7. Tail, 8. Tail fin.
	\end{figure}
	
	\begin{figure}[H]
	\begin{center}
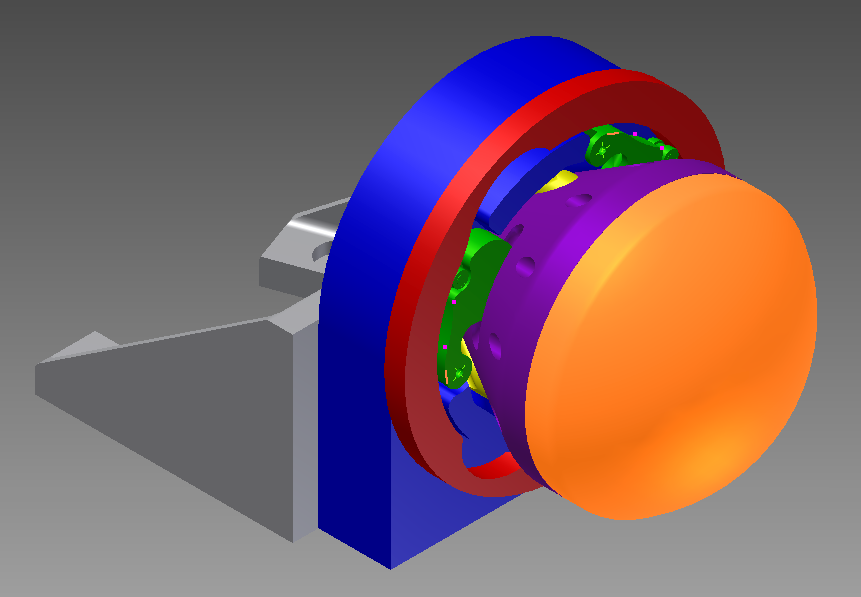
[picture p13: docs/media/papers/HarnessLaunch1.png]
		
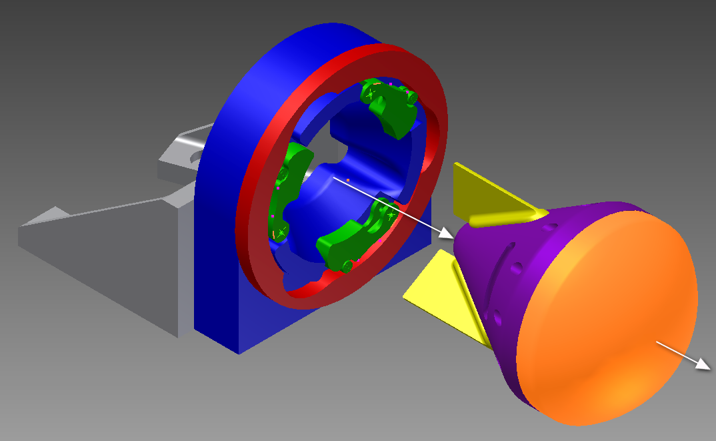
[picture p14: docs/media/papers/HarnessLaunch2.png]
		\\
	\end{center}
		\caption{}
		\label{ejection}
Capsule ejection sequence\\ The capsule (purple/orange) is held within the harness (blue) and secured by the latches (green). When the ejection sequence is initiated, the cam (red) rotates to allow the latches to release the capsule, allowing the spring (not visible) to push the capsule out of the harness.
	\end{figure}

\newpage
	\begin{figure}[H]
	\begin{center}
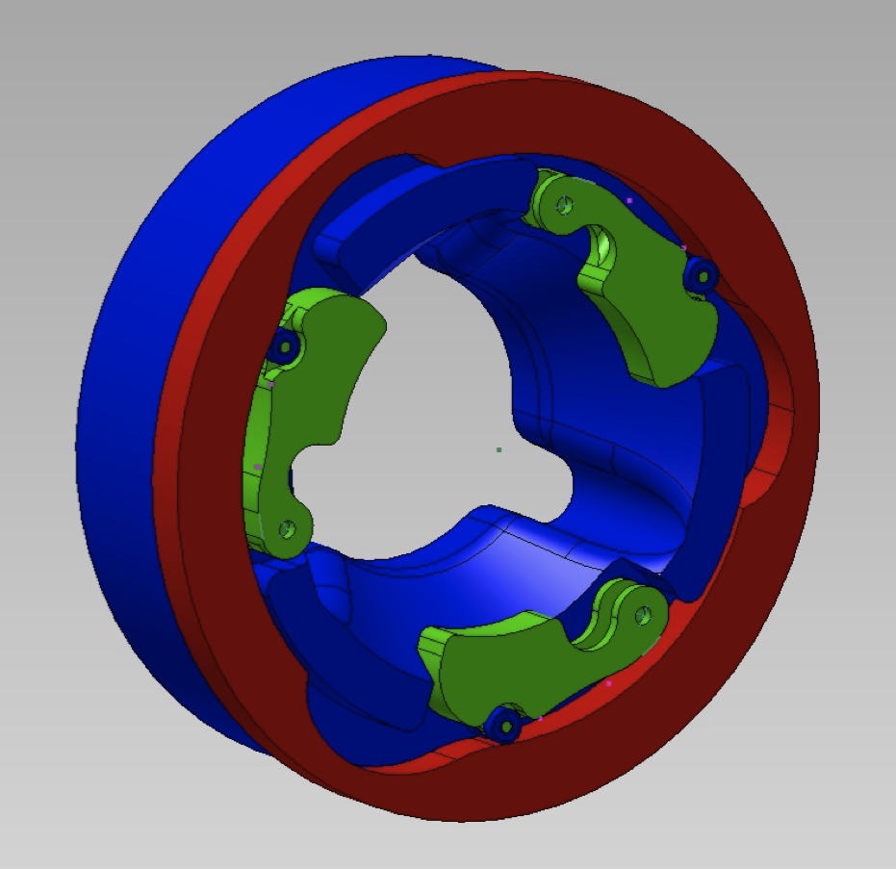
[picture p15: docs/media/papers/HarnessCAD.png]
		\\
	\end{center}
		\caption{}
		\label{harness}
Capsule harness/locking system\\ The shape of the capsule harness' (blue) interior is the negative of a cone, and cradles the capsule's tail and tail fins. The latches (green) slide into the slots located on the side of the capsule's tail, allowing the latches to lock the capsule in place within the harness. To release the capsule, the cam (red) rotates to allow the latches to hinge outward. The latches are spring-loaded, and so they are forced outward, releasing the capsule. (Refer to Figure \ref{capsule} for information on the capsule)
	\end{figure}

	\begin{figure}[H]
	\begin{center}
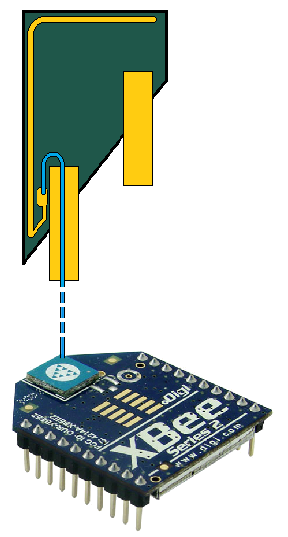
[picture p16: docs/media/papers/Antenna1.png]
		\hspace{1cm}
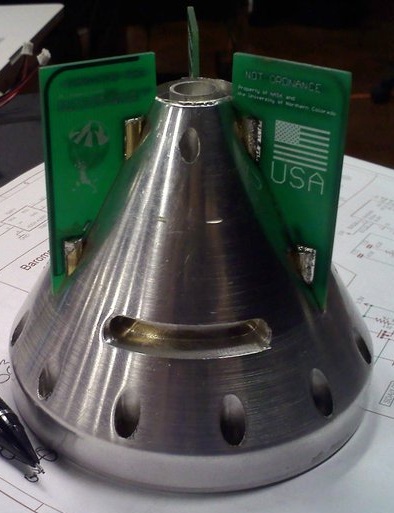
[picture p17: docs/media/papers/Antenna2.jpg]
		\\
	\end{center}
		\caption{}
		\label{antenna}
Tail fin antenna\\ The tail fins on the tail of the capsule were made of printed circuit board. Printed on the tail fin was a thin copper trace that was connected to a XBee radio within the capsule shell. The trace was cut down to a size that optimized signal transmission.
	\end{figure}

\newpage
	\begin{figure}[H]
	\begin{center}
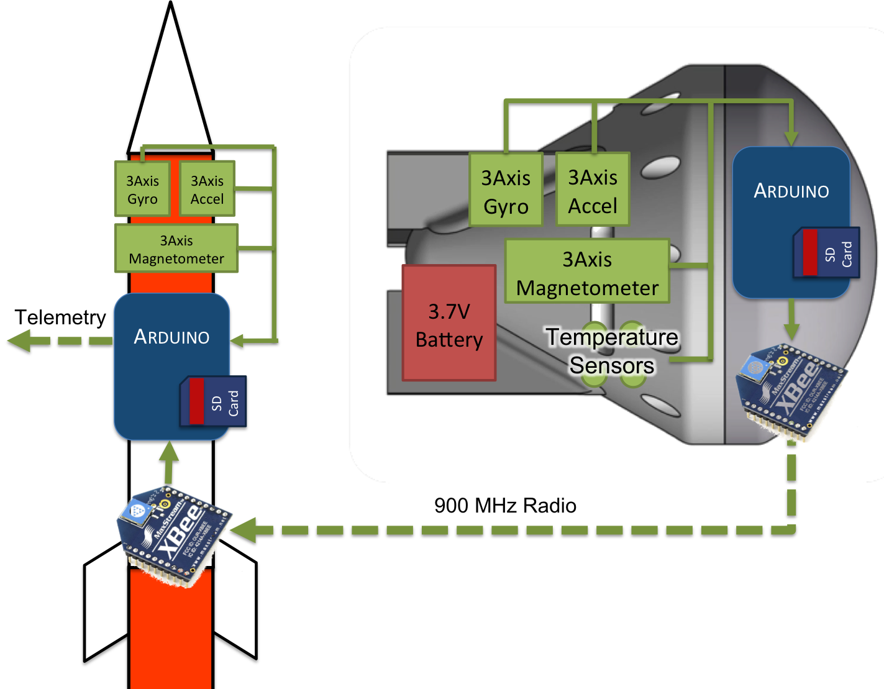
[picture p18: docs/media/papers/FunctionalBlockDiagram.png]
		\\
	\end{center}
		\caption{}
		\label{FBD}
Functional block diagram of the payload's electronics\\ This diagram includes the basic concept of operations for the payload's power distribution and data transfer along with the sensors and computers used to regulate the transfer of data.
	\end{figure}

	\begin{figure}[H]
	\begin{align*}
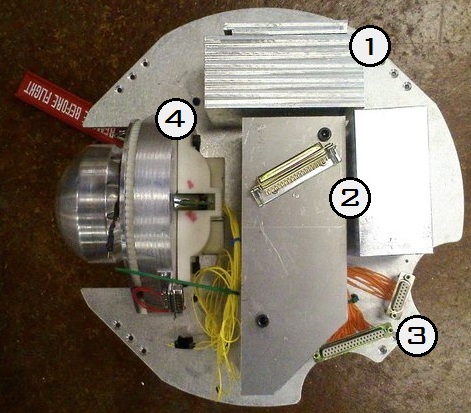
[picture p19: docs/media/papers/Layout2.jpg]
		&&\hspace{1cm}
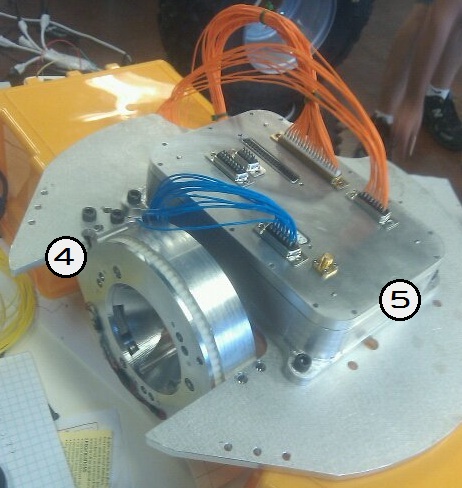
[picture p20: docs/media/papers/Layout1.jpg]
		\\
		Top~Side & &Bottom~Side
	\end{align*}
		\caption{}
		\label{layout}
Payload layout\\ The top side (facing toward the nose of the rocket) of the payload holds the GoPro camera box (1), mass ballast (2), the power/telemetry interface to the rocket (3), and the capsule harness (4) (the white plastic behind the harness houses the ejection spring and capsule umbilical). The bottom side holds the electronics box (5).
	\end{figure}

\newpage
	\begin{figure}[H]
	\begin{center}
		(A.)
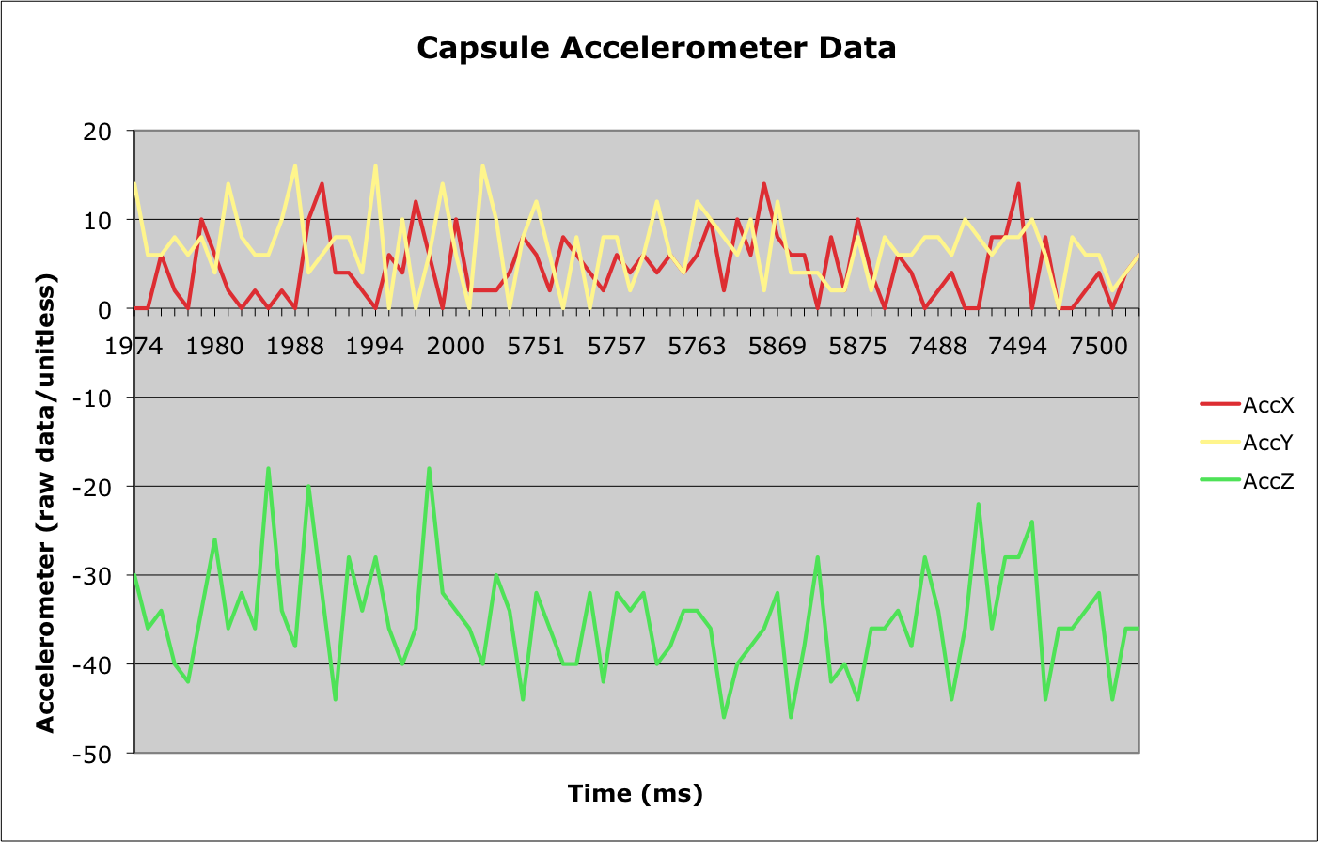
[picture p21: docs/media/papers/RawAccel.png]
		\\
		(B.)
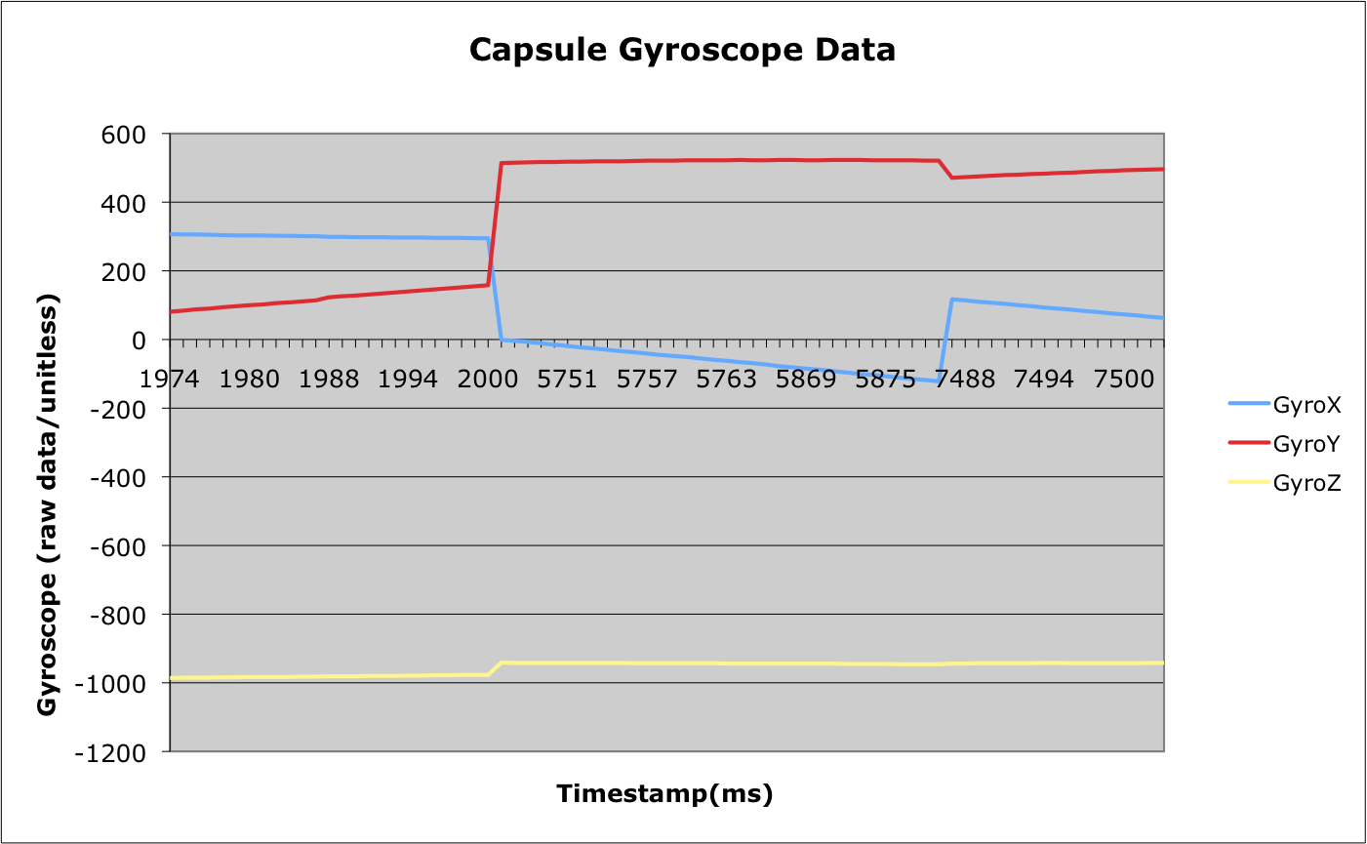
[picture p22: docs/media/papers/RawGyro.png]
		\\
		(C.)
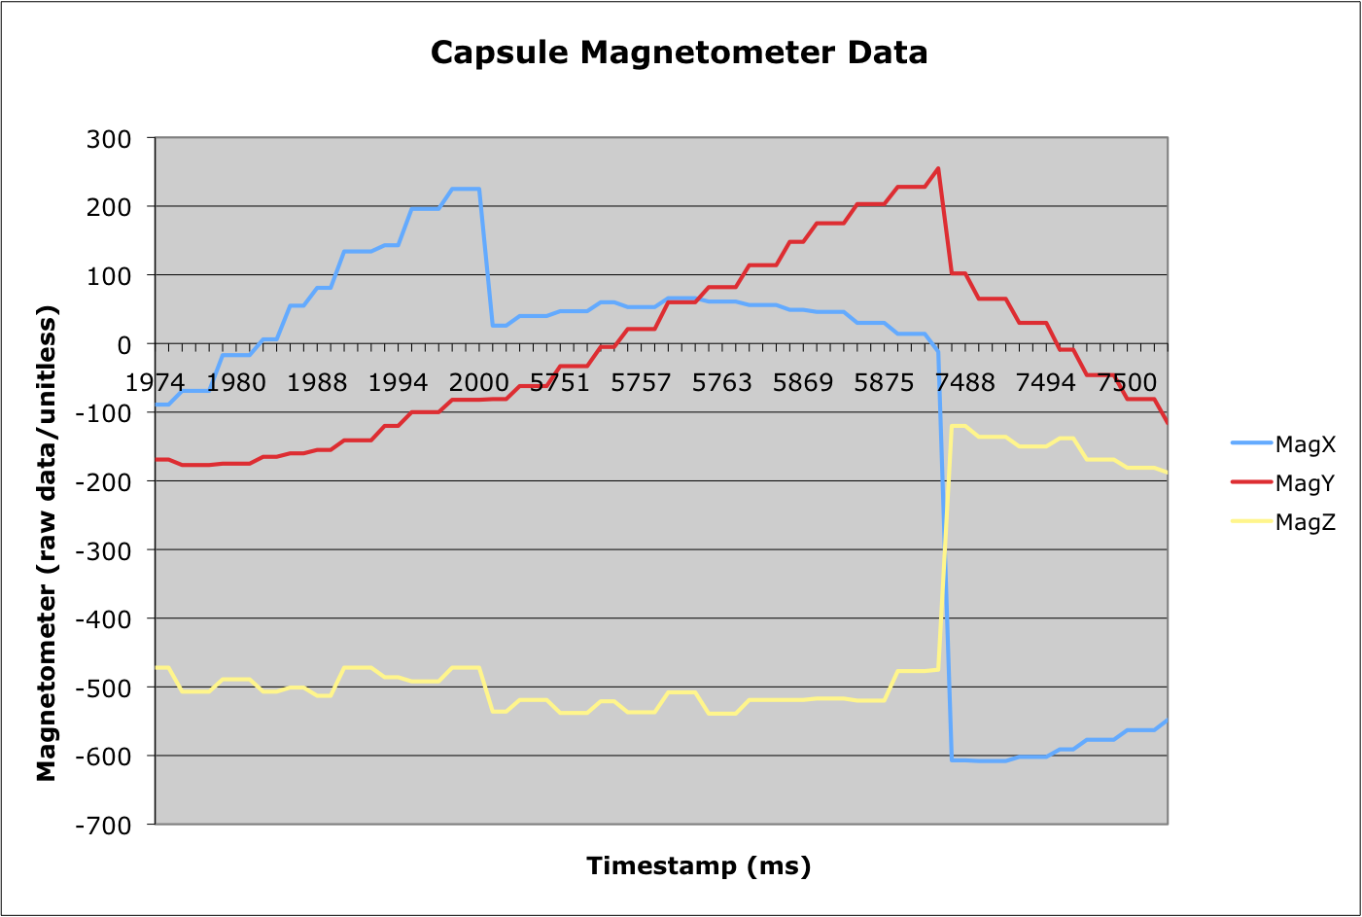
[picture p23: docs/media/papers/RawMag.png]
		\\
	\end{center}
		\caption{}
		\label{raw}
Recovered flight data\\ The above plots are IMU sensor data from the capsule. The plots show the same time interval (approximately 6 seconds long) which was recorded immediately following fairing ejection/capsule initialization. While the accelerometer data (A) does not present any noticeable trends, it is interesting to note that there are significant events that occur in plots B and C at time +2s and +7.5s. This suggests that the sensors were recording physical movement of some kind, although not enough information was gathered to accurately determine what event this might signify.
	\end{figure}
\newpage

\end{document}

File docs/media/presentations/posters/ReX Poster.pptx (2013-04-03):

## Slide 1

Rocket SAT
UNC Physics was involved with a project called Rocket SAT-X, an outreach program funded by the Colorado Space Grant Consortium (COSGC). This program challenged students to design and fabricate an experimental payload that was launched on a Terrier-Orion sounding rocket, provided and launched by NASA’s Wallops Flight Facility in Virginia. The rocket flight launched the payloads approximately 120km into space, where the rocket then shed its fairing, exposing the student payloads to the space environment (Figure 1).

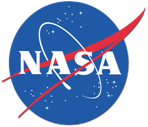
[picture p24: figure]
36991_1506316264165_1422042014_1307303_1729622_n

Abstract

University of Northern Colorado

Reentry Experiment SAT-X

M. Woods, A. Adamson, J. Aken, M. Honda, C. Kuhns, & R. Shiely
Advisors: C. Galovich, M. Semak, & R. Walch


Design Methods Material and Data Recovery

The mathematical model presents two design issues:
- Heat buildup due to air friction may cause breakup or melting.
- The capsule may not survive the extreme force of impact at splashdown
Unfortunately, accounting for one amplifies the other, i.e., reducing the drag decreases the total heat buildup yet increases the capsule’s impact velocity. Therefore, the capsule was machined from 6061 Aluminum (using an automated CNC mill) and reflected the design in Figure 2. Aluminum provided a strong, supportive material that was light and that could absorb large amounts of thermal energy.
Data may not be retrievable because of burn-up on reentry, destruction on impact, or inability to recover the capsule. To ensure data capture, a set of 900MHz XBee radio transceivers continuously transmitted information from the capsule to the ground via the base station on the rocket (Figure 6). Antennae were embedded within the tailfins (which were made of PCB) to maximize the capsule-rocket wireless connection.

Figure 6. Functional Block Diagram

The University of Northern Colorado Reentry Experiment SAT-X (ReX) project was designed to shed light on the challenging process of atmospheric reentry. The experiment was conducted using a small reentry capsule, jettisoned at apogee from a sounding rocket. The flight tested the capability of the capsule as a platform for future reentry experiments.

Design Methods Reentry Capsule Shell & Base Station

“Bomb” Model

Sphere Model

Apollo Capsule

Streamlined Model

Each of the above models was constructed and evaluated for: aerodynamic stability, self-orienting characteristics, structural integrity, internal storage space for electronics, and drag coefficient. The evaluation was carried out by conducting several short-range drop tests and using a CAD simulation and the mathematical model. With this, the streamline shaped model proved to be the most suitable candidate for an effective reentry vehicle.
Figure 2 shows the entire ReX payload. The capsule contains two electronics and sensor boards and radio antennae are embedded in the tail fins. A harness/lock holds the capsule in place until an external timing signal triggers the unlocking sequence. The capsule is then ejected by a spring loaded plunger. An HD camera is used to record the capsule launch. All of these subsystems are integrated on the rocket-mounted deck plate.


2

1

3

Reentry Capsule
Capsule Harness/Lock
Accelerator (Spring/Plunger)
“Go Pro” HD Camera Housing
Rocket-Mounted Deck Plate


3

2

4

1

5

1

2

Theory and Scientific Concepts

The analytical model estimates the force of impact and the effects of heat during reentry. It was used to refine the shape of the capsule (Figure 2) and to interpret the flight data.
The model requires a knowledge of the forces exerted on the reentry vehicle. The dominant force is air resistance. Assuming a purely vertical descent, the resultant acceleration due to air drag and gravity results in the following equation:
Using this equation, the capsule’s velocity versus altitude can be plotted. This is the blue curve in Figure 3.
Figure 3. Reentry vehicle dropped from 120km
The green curve describes the motion of a freely falling object. The red curve is the altitude-dependent terminal velocity. At higher altitudes, where there is virtually no drag, the object is effectively freely falling as indicated by the convergence of the blue and green curves.
At the point where the terminal velocity and free fall curves cross, the capsule experiences a significant change in velocity. The change is abrupt, as illustrated by the velocity and acceleration profiles in Figure 4. This phenomenon can be compared to that of an object hitting a “wall of atmosphere”. The “impact” causes the reentry object to experience a large impulse and heat buildup due to air friction. Both effects could prove hazardous to the capsule.
The curve in Figure 5 is generated by calculating the power as a function of time using the drag force and capsule’s velocity. The area under the curve is potentially the heat transferred to the capsule.

Figure 4. Reentry vehicle dropped from 120km

Figure 5. Heat Energy of Reentry

Power Shade R

Mission Introduction
“To provide a method for institutions to utilize a deployable and recoverable payload for future Rocket SAT-X missions. By providing this, we can greatly increase the amount of data recovered by eliminating the need to transmit restricted amounts of data to the ground.”
ReX aimed to characterize the process of reentry via data collected from a capsule ejected from a sounding rocket at apogee. Inertial data was used to reconstruct the actual trajectory, as well as to profile the drag force. In the absence of the actual data, a mathematical model (outlined in Theory and Scientific Concepts) was constructed to inform the initial capsule design. Data collected from the flight was used to optimize the model, thereby facilitating further refinement of the capsule design. By optimizing the payload design, fewer resources may be used in payload fabrication, saving time and money. Finally, this tested platform can be used by future reentry experiments, as the design and fabrication process have been refined by the ReX team.

1.Launch
2.Ascent: Onboard electronics initialize
3.Apogee: Fairing deployment; ReX capsules deployed
4.Decent: ReX capsules collect reentry data; Data transmitted to rocket
5.Splashdown

VH
terminal vfree

Results and Discussion

Recovery of the ReX payload after mission termination and splashdown suggested that the capsule was ejected properly at apogee. Successful ejection was confirmed by the recovery of onboard video footage of the rocket body after fairing separation. The reentry capsule body has still not been recovered. Physical examination of the recovered rocket payload section showed that the payload's computer and electronics box did not survive the flight and was missing altogether. Evidence of scraps and buffs in the aluminum deck plate and on the aluminum container of the UW AstroX payload (located directly beneath the ReX payload) suggested that the computer box liberated itself from the rocket. This may have been caused by splashdown or the unexpectedly high temperatures experienced by the rocket during reentry.
Telemetry data collected and recorded by Wallops Flight Facility suggested that the ReX payload failed to collect any useful inertial data from any of the capsule's sensors. The telemetry log showed that the payload's umbilical to the capsule (designed to turn on the capsule computer and confirm capsule connectivity to the rocket) were operational until capsule separation. After ejection, the capsule's sensors were functional for only six seconds, after which time only intermittent signals were received

1

2

3

4

5


Figure 1

Figure 2

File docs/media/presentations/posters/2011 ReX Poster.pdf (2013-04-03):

# MISSION

“TO PROVIDE A METHOD FOR INSTITUTIONS TO UTILIZE A

DEPLOYABLE AND RECOVERABLE PAYLOAD FOR FUTURE ROCKET SAT-X MISSIONS. BY PROVIDING THIS, WE CAN

GREATLY INCREASE THE AMOUNT OF DATA RECOVERED BY

ELIMINATING THE NEED TO TRANSMIT RESTRICTED AMOUNTS OF DATA TO THE GROUND.”

ReX aims to characterize the process of reentry via data collected from a pair of capsules ejected from a sounding rocket at apogee. Inertial data will be used to reconstruct the actual trajectory, as well as to profile the drag force. Thermal data will be used to map the heat distribution over the capsule surface. In the absence of the actual data, a mathematical model (outlined in Theory and Scientific Concepts) was constructed to inform the initial capsule design. Data collected from the flight will be used to optimize the model, thereby facilitating further refinement of the capsule design. Some aerospace
missions | tend | to | over-engineer | flight | hardware, | designing
components to standards that are well beyond what is necessary. By optimizing the payload design, fewer resources may be used in payload fabrication, saving time and money. Finally, the revised platform can be used by future reentry experiments.

# UNIVERSITY of NORTHERN COLORADO

# REENTRY EXPERIMENT SAT-X

ABSTRACT

# THEORY AND SCIENTIFIC CONCEPTS

# ROCKET SAT

UNC Physics has become involved with a project called Rocket SAT-X, an outreach program funded by the Colorado Space Grant Consortium (COSGC). This program challenges students to design and fabricate an experimental payload that will be launched on a Terrier-Orion sounding rocket, provided and launched by NASA’s Wallops Flight Facility in Virginia. The rocket flight will launch the payloads approximately 120km into space, where the rocket will then shed its fairing, exposing the student payloads to the space environment, as shown in FIGURE 1.

### 1. LAUNCH

## 2. ASCENT: Onboard electronics initialize

## 3. APOGEE: Fairing deployment; ReX capsules deployed

4. DESCENT: ReX capsules collect reentry data;

## Data transmitted to rocket

### 5. SPLASHDOWN

FIGURE 1

## DESIGN REENTRY CAPSULE SHELL& BASE STATION

Each of the above models was constructed and evaluated for: aerodynamic stability, self-orienting characteristics, structural integrity, internal storage space for electronics, and drag coefficient. The evaluation was carried out by conducting several short-range drop tests and using a CAD simulation and the mathematical model. With this, the streamline shaped model proved to be the most suitable candidate for an effective reentry vehicle.

Figure 2 shows the entire ReX payload. The capsule contains two electronics and sensor boards and radio antennae are embedded in the tail fins. A harness/lock holds the capsule in place until an external timing signal triggers the unlocking sequence. The capsule is then ejected by a spring loaded plunger. An HD camera is used to record the capsule launch. All of these subsystems are integrated on the rocket-mounted deck plate.

## The University of Northern Colorado Reentry Experiment SAT-X (ReX) project is designed to

shed light on the challenging process of atmospheric reentry. The experiment will be conducted using a small reentry capsule, jettisoned at apogee from a sounding rocket. The flight will test the capability of the capsule as a platform for future reentry experiments.

## DESIGN HEAT SHIELD AND DATARECOVERY

“BOMB” MODEL | SPHERE MODEL | APOLLO CAPSULE | STREAMLINED MODEL

The analytical model estimates the force of impact and the effects of heat during reentry. It is used to refine the shape of the capsule (Figure 2) and to interpret the flight data.

The model requires a knowledge of the forces exerted on the reentry vehicle. The dominant force is air resistance. Assuming a purely vertical descent, the resultant acceleration due to air drag and gravity results in the following equation:

where g(h) is Earth's gravitational acceleration with respect to altitude, ρ(h) is the air
density with respect to altitude, | is the capsule’s speed, A and m are the capsule’s
cross-sectional area and mass, respectively, and Cd is the geometry-dependent drag coefficient.

Using this equation, the capsule’s velocity versus altitude can be plotted. This is the blue curve in Figure 3.


Figure 3. Reentry vehicle dropped from 120km

The green curve describes the motion of a freely falling object. The red curve is the altitude-dependent terminal velocity. At higher altitudes, where there is virtually no drag, the object is effectively freely falling as indicated by the convergence of the blue and green curves.

At the point where the terminal velocity and free fall curves cross, the capsule experiences a significant change in velocity. The change is abrupt, as illustrated by the velocity and acceleration profiles in Figure 4. This phenomenon can be compared to that of an object hitting a “wall of atmosphere”. The impact causes the reentry object to experience a large impulse and heat buildup due to air friction. Both effects could prove hazardous to the capsule.

The curve in Figure 5 is generated by calculating the power as a function of time using the drag force and capsule’s velocity. The area under the curve is potentially the heat

The mathematical model makes two design issues apparent:

- The capsule may not survive the extreme force of impact at splashdown
- Heat buildup due to air friction may cause breakup or melting

Unfortunately, accounting for one amplifies the other, i.e., reducing the drag decreases the total heat buildup yet increases the capsule’s impact velocity. This conflict was addressed by adding a heat shield. The carbon fiber heat shield protects the heat-sensitive aluminum. By leaving the capsule shape intact, the drag coefficient is unaffected and the impact velocity is unchanged.

Figure 6 (left) shows a test of a heat shield in which aluminum is coated with graphite epoxy and overlaid with carbon-fiber. It is then heated over a set period of time. Two other samples were tested - bare aluminum and aluminum coated in graphite epoxy. Initially, the rate of temperature change was least for the carbon fiber coated sample. The math model shows that heat acquisition occurs over a short time, so it’s adequate to consider the initial behavior of the temperature. Therefore, the best heat shield is the carbon-fiber/graphite epoxy coating.

Data may not be retrievable because of burn-up on reentry, destruction on impact, or inability to recover the capsule. To ensure data capture, a set of 900MHz XBee radio transceivers continuously transmit information from the capsule to the ground via the base station on the rocket.

FIGURE 6

FIGURE 7. FUNDIMENTAL BLOCK DIAGRAM

# MANUFACTURING

The UNC team is fabricating the various capsule bodies and launchers
and | assembling | the | required
electronics (Figure 8).

The mechanical elements, including the capsule, the capsule launcher/ locking harness, the RS-X deck mounts, and the camera housing will be fabricated out of 6061 Aluminum, and will be machined using an automated CNC mill (Figure 9). A
Rapid | Prototyper | plastic | printing
machine at Road Narrows Robotics was used to create a prototype model (Figure 10) of the capsule for preliminary testing.

The payloads’ custom electronics boards will be printed by Advanced Circuits. Once these are printed, the appropriate sensors, computers, and radios will be assembled on the boards, which will then be integrated into the reentry capsule shells.


Figure 4. Reentry vehicle dropped from 120km | Figure 5. Heat Energy of Reentry

1

2

3

## Reentry Capsule Capsule Harness/Lock

Accelerator (Spring/Plunger)

## “Go Pro” HD Camera Housing Rocket-Mounted Deck Plate

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
FIGURE 2

Figure 8

Figure 9

Figure 10

Road Narrows Robotics,
Loveland, CO

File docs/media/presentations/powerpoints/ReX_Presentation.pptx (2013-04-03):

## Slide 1


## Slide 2


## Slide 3


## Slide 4


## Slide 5

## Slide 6


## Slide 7


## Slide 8

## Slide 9


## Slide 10


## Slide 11

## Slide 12


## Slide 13


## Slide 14


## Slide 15


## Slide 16

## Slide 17


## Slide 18


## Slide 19


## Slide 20

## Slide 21


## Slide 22


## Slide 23


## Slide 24

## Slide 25


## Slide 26


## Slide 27


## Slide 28

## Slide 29

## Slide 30


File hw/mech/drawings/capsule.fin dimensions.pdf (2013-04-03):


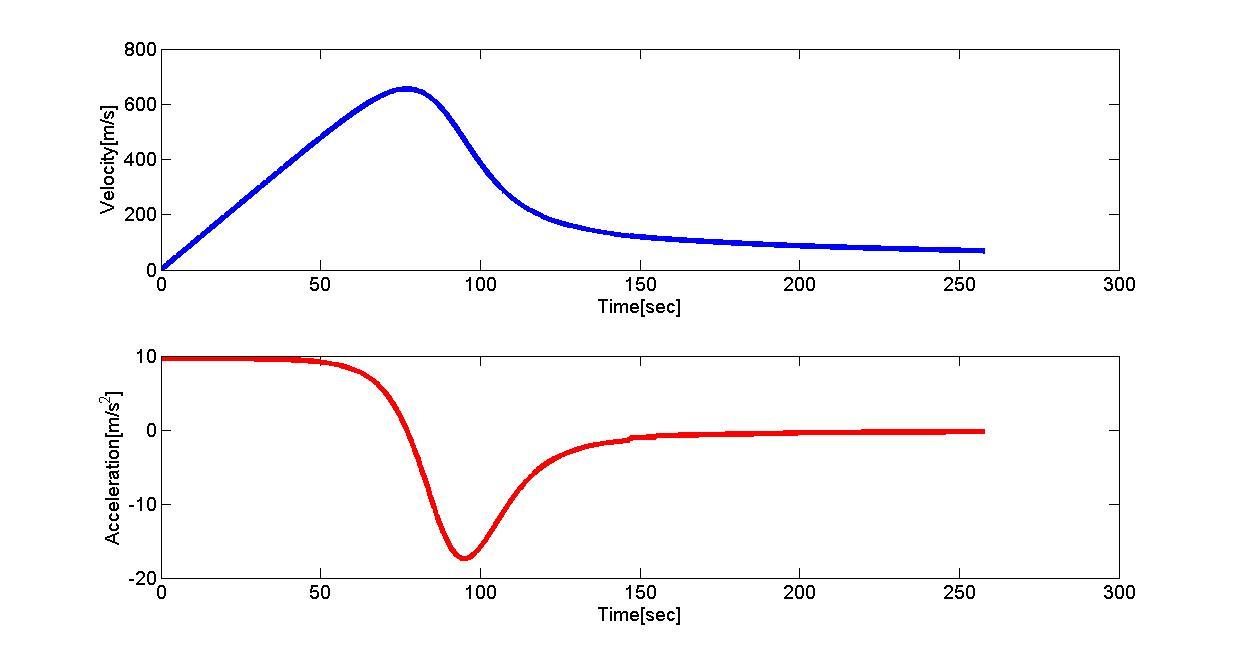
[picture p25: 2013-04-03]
docs/media/papers/KinematicsBallDrop_60km.jpg

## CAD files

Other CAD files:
hw/mech/ANSI B18.3.1M(6)/ANSI B18.3.1M - M1.6x0.35 x 3(1).ipt
hw/mech/ANSI B18.3.1M(6)/ANSI B18.3.1M - M2.5x0.45 x 10(1).ipt
hw/mech/ANSI B18.3.1M(6)/ANSI B18.3.1M - M2.5x0.45 x 12(1).ipt
hw/mech/ANSI B18.3.1M(6)/ANSI B18.3.1M - M2.5x0.45 x 16(1).ipt
hw/mech/ANSI B18.3.1M(6)/ANSI B18.3.1M - M2.5x0.45 x 4(1).ipt
hw/mech/ANSI B18.3.1M(6)/ANSI B18.3.1M - M2.5x0.45 x 5(1).ipt
hw/mech/ANSI B18.3.1M(6)/ANSI B18.3.1M - M2.5x0.45 x 6(1).ipt
hw/mech/ANSI B18.3.1M(6)/ANSI B18.3.1M - M2.5x0.45 x 8(1).ipt
hw/mech/ANSI B18.3.1M(6)/ANSI B18.3.1M - M2x0.4 x 10(1).ipt
hw/mech/ANSI B18.3.1M(6)/ANSI B18.3.1M - M2x0.4 x 12(1).ipt
hw/mech/ANSI B18.3.1M(6)/ANSI B18.3.1M - M2x0.4 x 3(1).ipt
hw/mech/ANSI B18.3.1M(6)/ANSI B18.3.1M - M3x0.5 x 10(1).ipt
hw/mech/ANSI B18.3.1M(6)/ANSI B18.3.1M - M3x0.5 x 12(1).ipt
hw/mech/ANSI B18.3.1M(6)/ANSI B18.3.1M - M3x0.5 x 20(1).ipt
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

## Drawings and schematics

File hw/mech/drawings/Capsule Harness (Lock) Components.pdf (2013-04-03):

## PRODUCED BY AN AUTODESK EDUCATIONAL PRODUCT

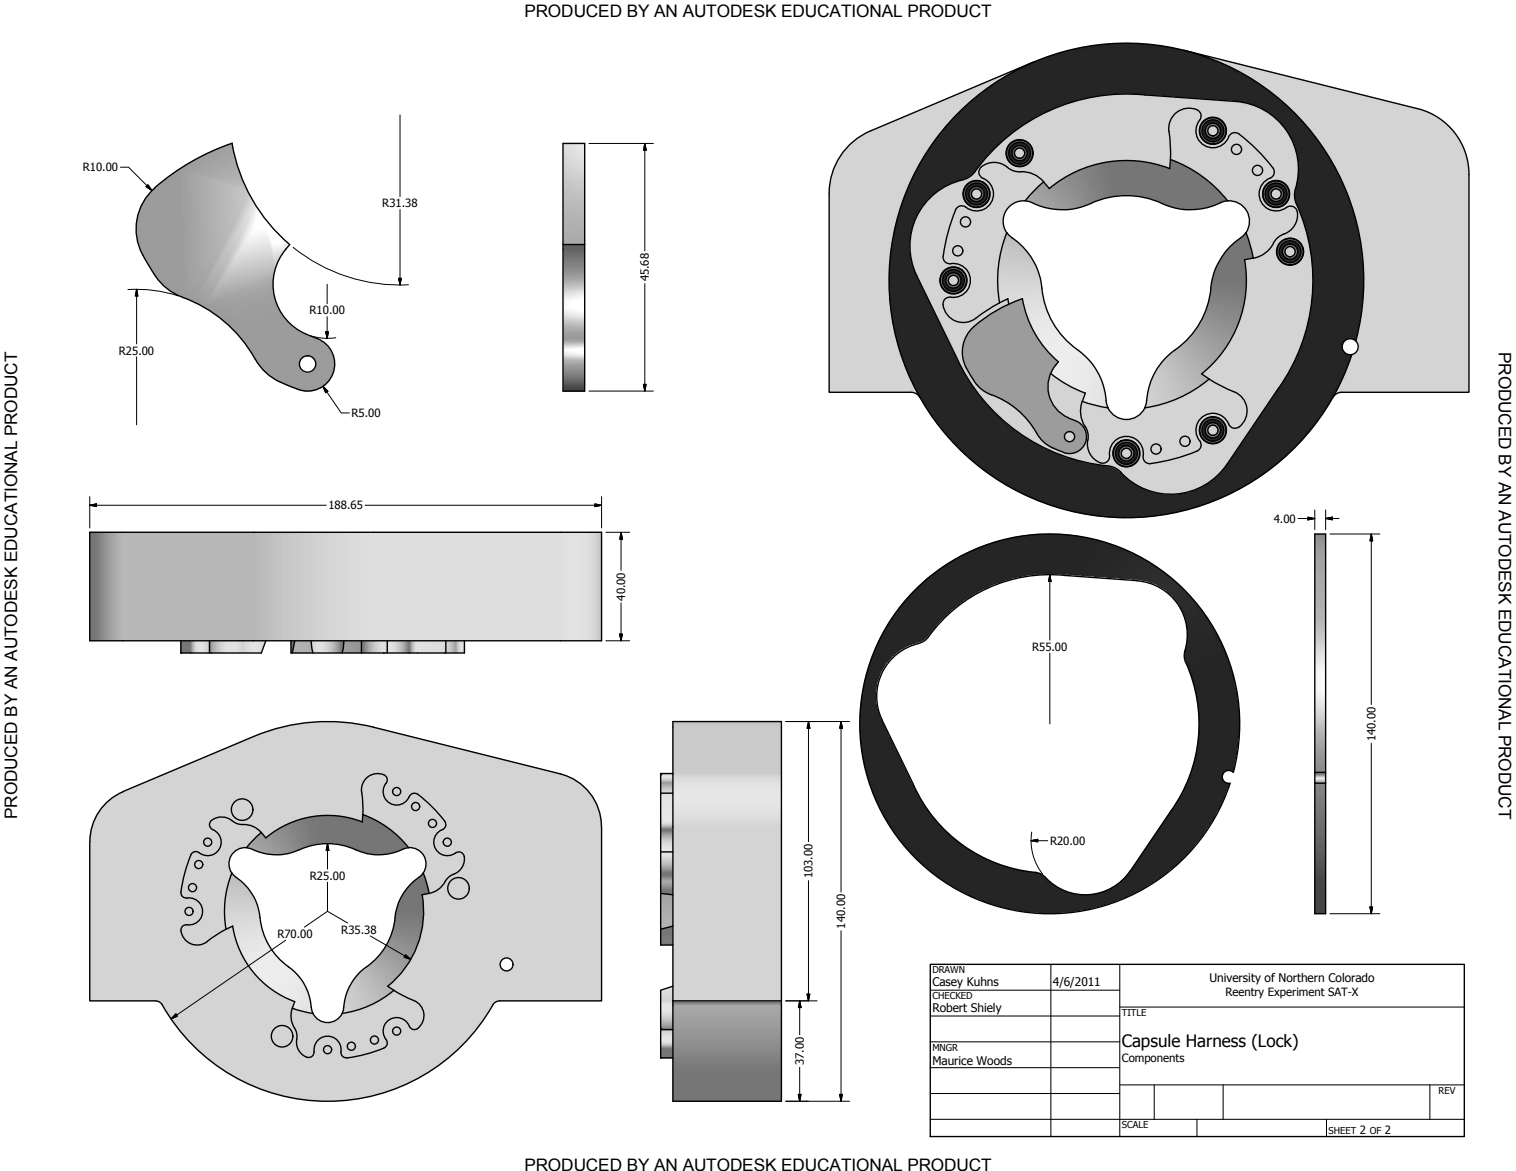
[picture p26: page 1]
TIO; P R O D U C E D B Y A N A U T O D E S K E D U C A TIO; SHEET 2 OF 2; DRAWN; CHECKED; MNGR Maurice Woods; Casey Kuhns; Robert Shiely; SCALE; REV

University of Northern Colorado
Reentry Experiment SAT-X

TITLE
Capsule Harness (Lock)
Components

PRODUCED BY AN AUTODESK EDUCATIONAL PRODUCT

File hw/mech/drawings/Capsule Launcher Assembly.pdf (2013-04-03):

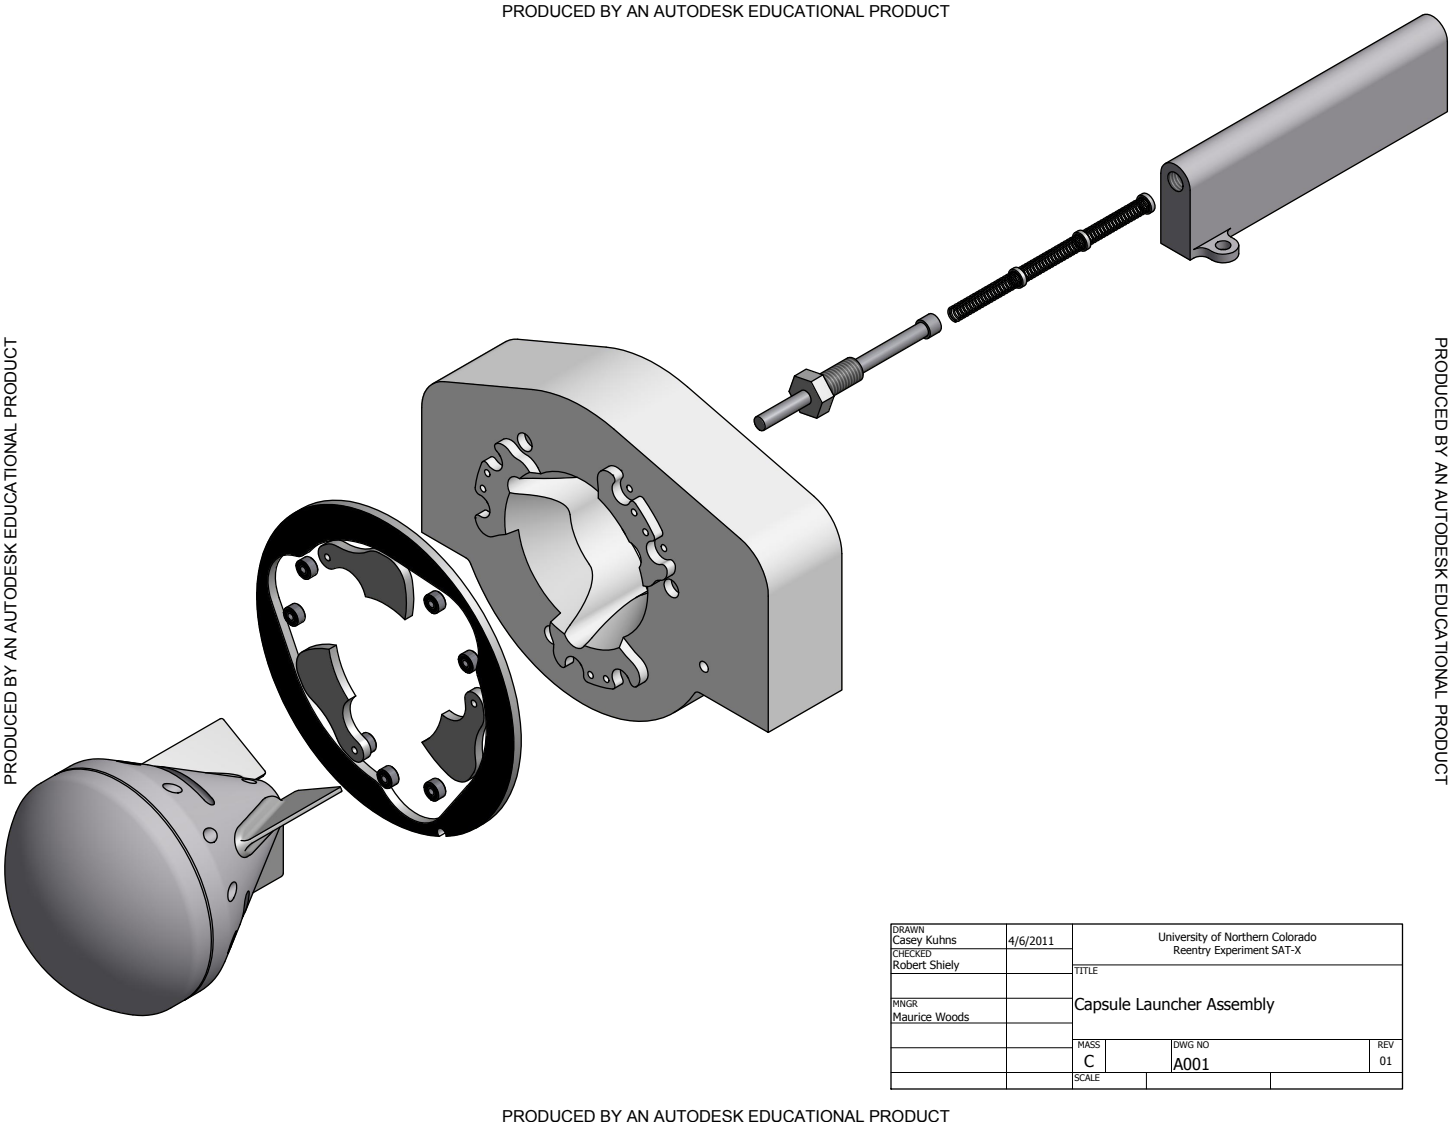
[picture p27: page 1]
TIO N; ely; ule; bly; olo

PRODUCED BY AN AUTODESK EDUCATIONAL PRODUCT

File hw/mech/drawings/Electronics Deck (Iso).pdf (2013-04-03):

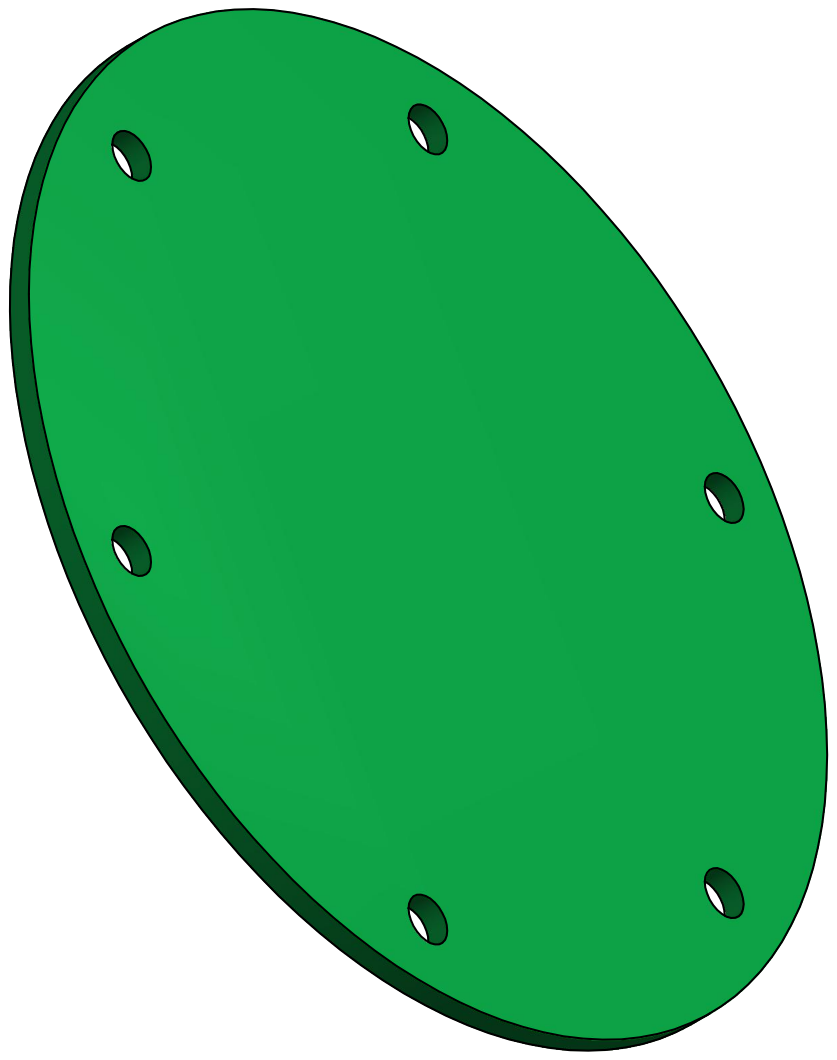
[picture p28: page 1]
SHEET 1 OF 2; DRAWN; MNGR Maurice Woods; Casey Kuhns; Robert Shiely; DWG NO Electronics Deck; TITLE; CAPSULE CAP; Electronics Deck

University of Northern Colorado
Reentry Experiment SAT-X

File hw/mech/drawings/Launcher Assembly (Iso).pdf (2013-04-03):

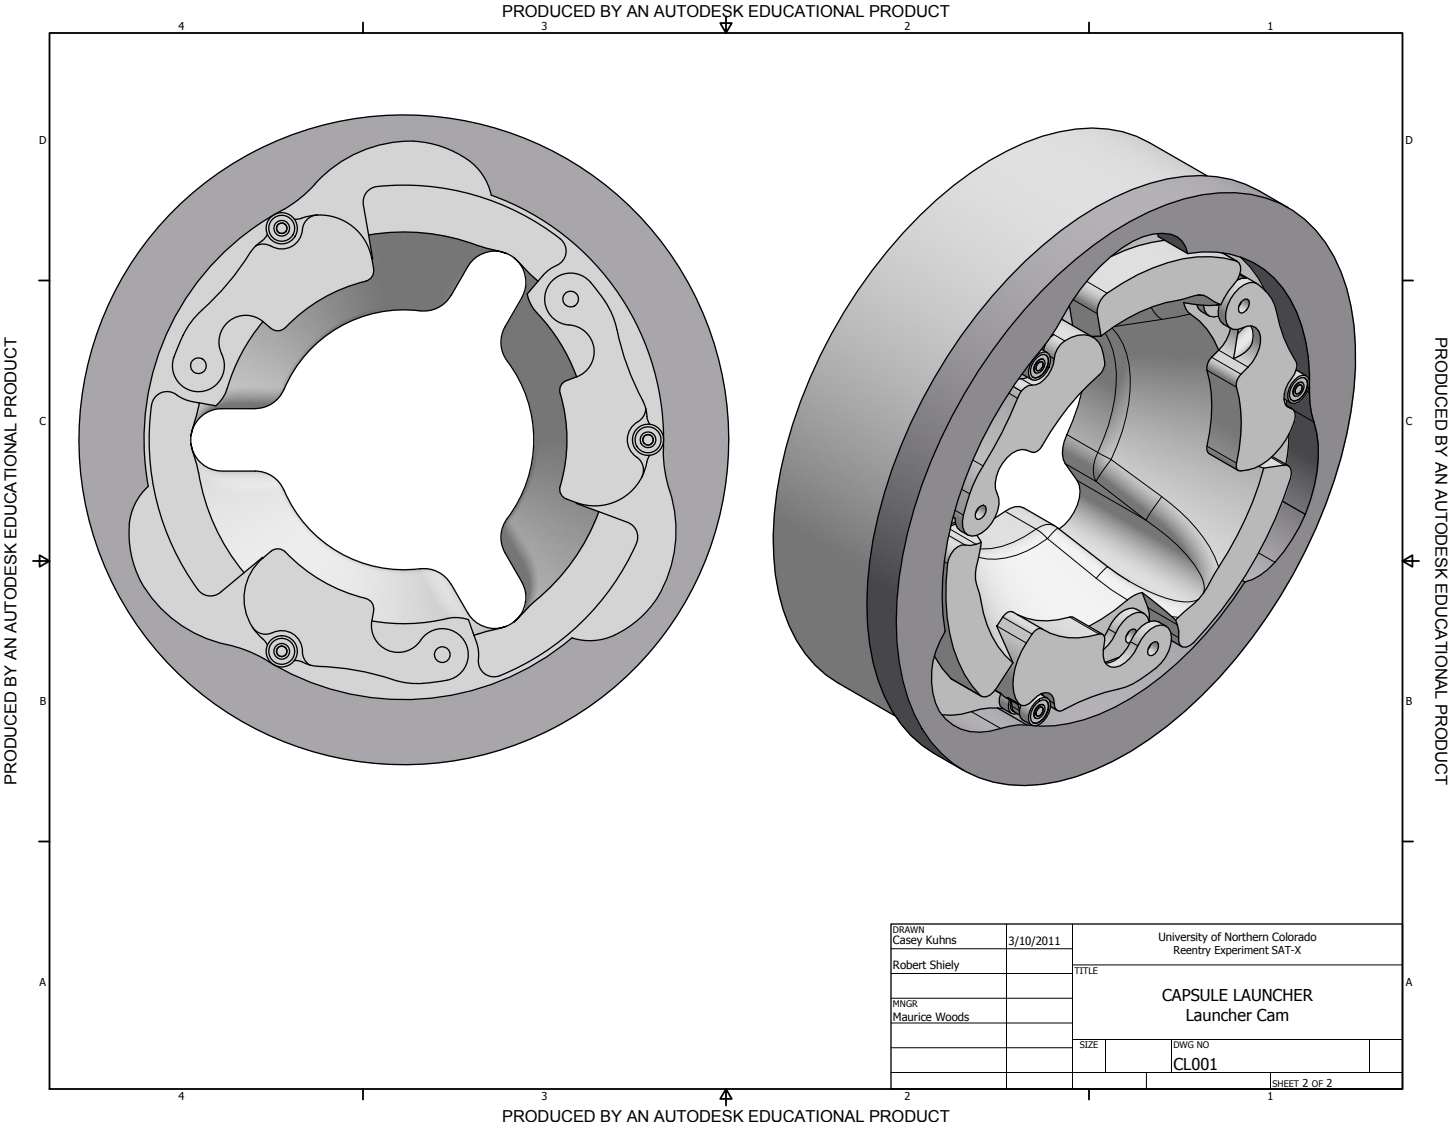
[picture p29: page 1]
TIO N; ely; olo

PRODUCED BY AN AUTODESK EDUCATIONAL PRODUCT

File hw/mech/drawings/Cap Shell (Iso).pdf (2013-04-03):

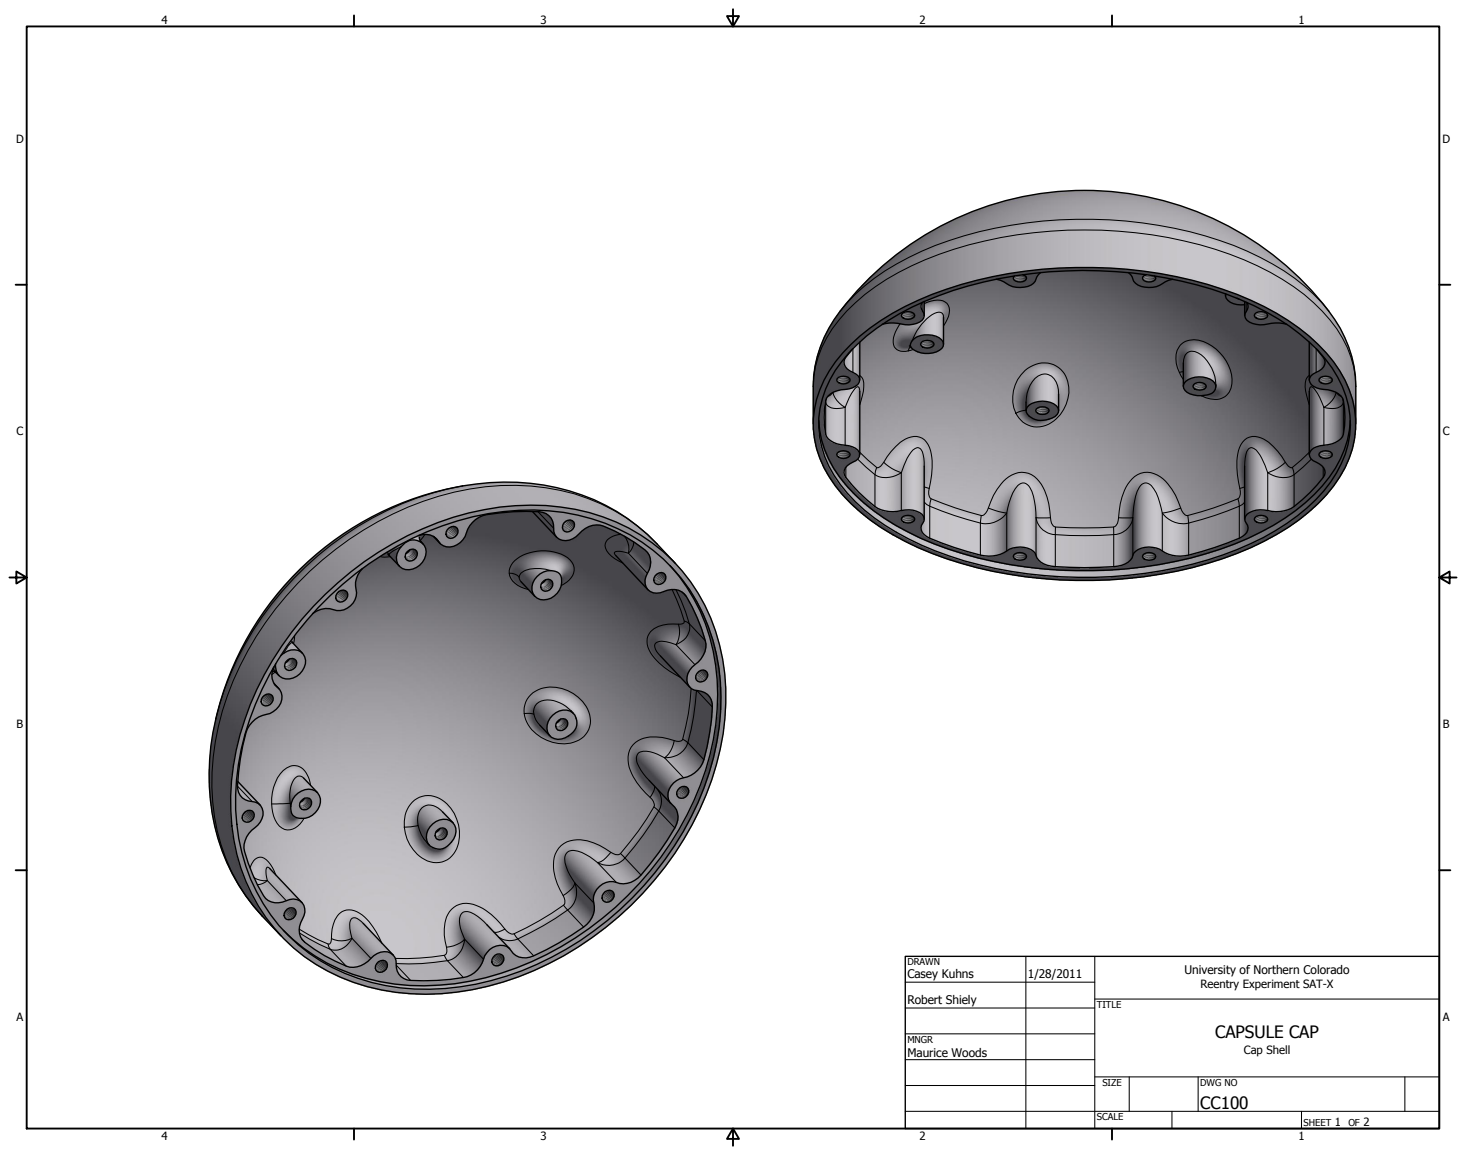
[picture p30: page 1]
SHEET 1 OF 2; DRAWN; MNGR Maurice Woods; Casey Kuhns; Robert Shiely; DWG NO CC100; TITLE; CAPSULE CAP; Cap Shell; SIZE; SCALE

University of Northern Colorado
Reentry Experiment SAT-X

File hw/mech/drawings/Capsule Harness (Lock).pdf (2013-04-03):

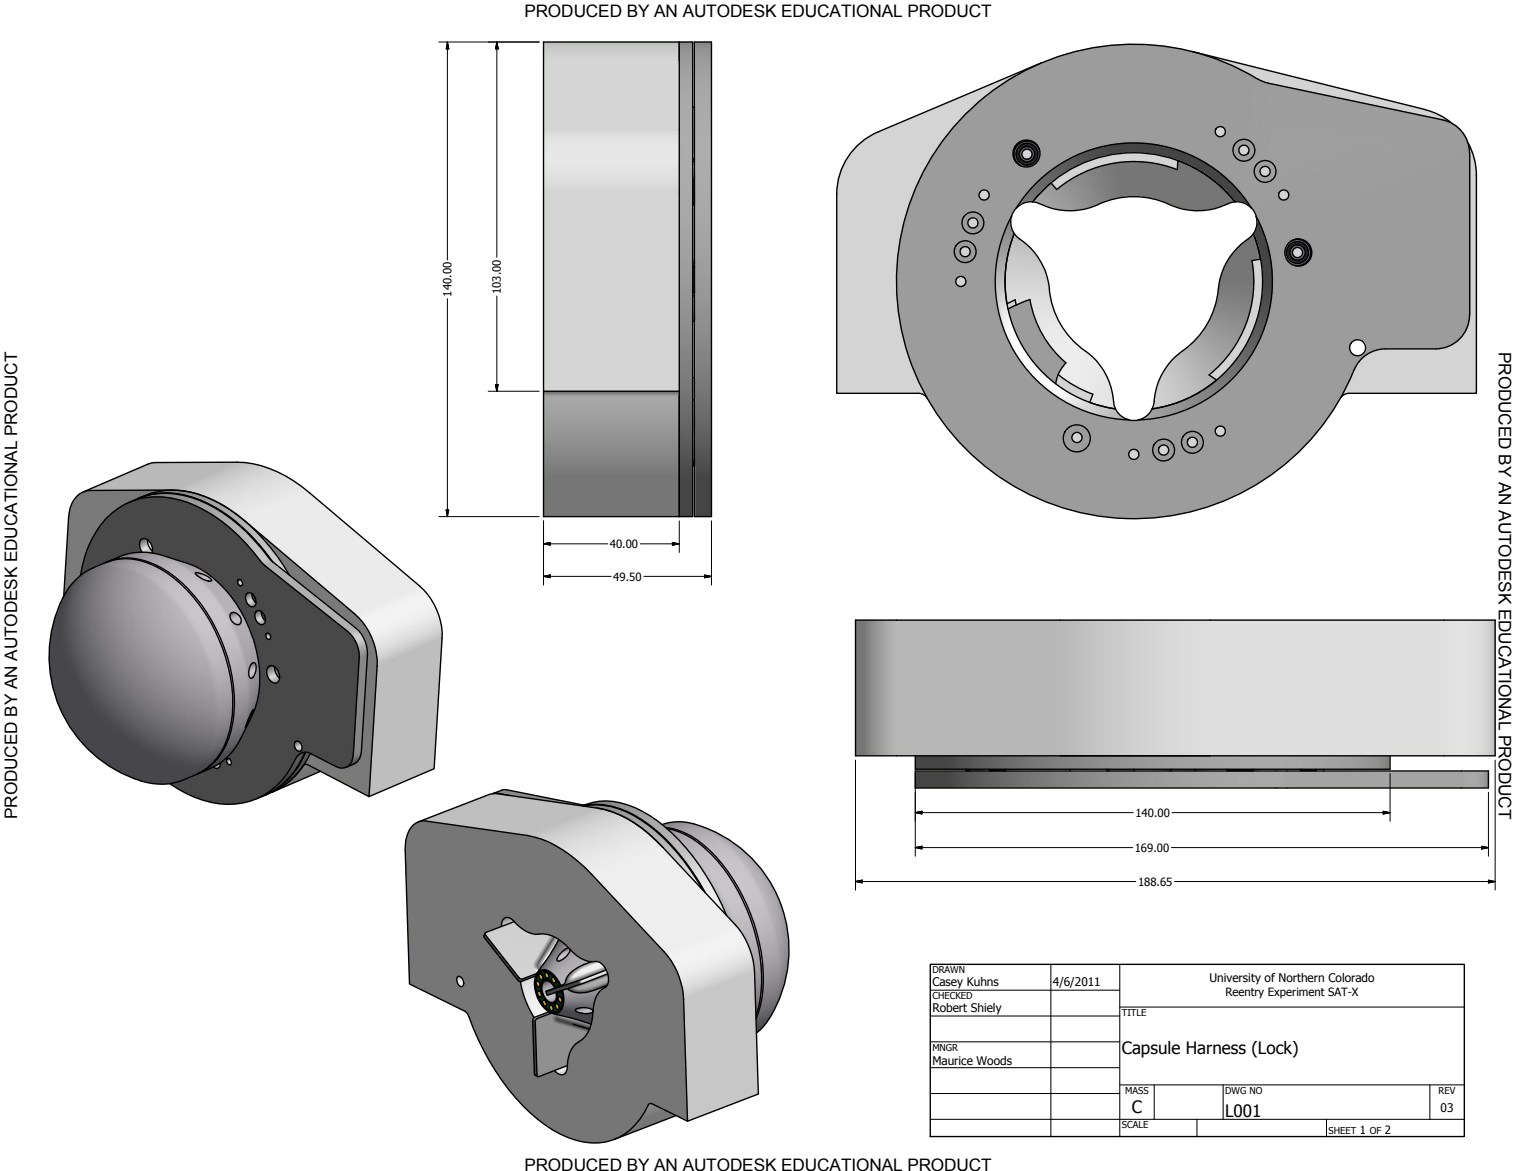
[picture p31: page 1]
TIO N; ely; ule; olo

PRODUCED BY AN AUTODESK EDUCATIONAL PRODUCT

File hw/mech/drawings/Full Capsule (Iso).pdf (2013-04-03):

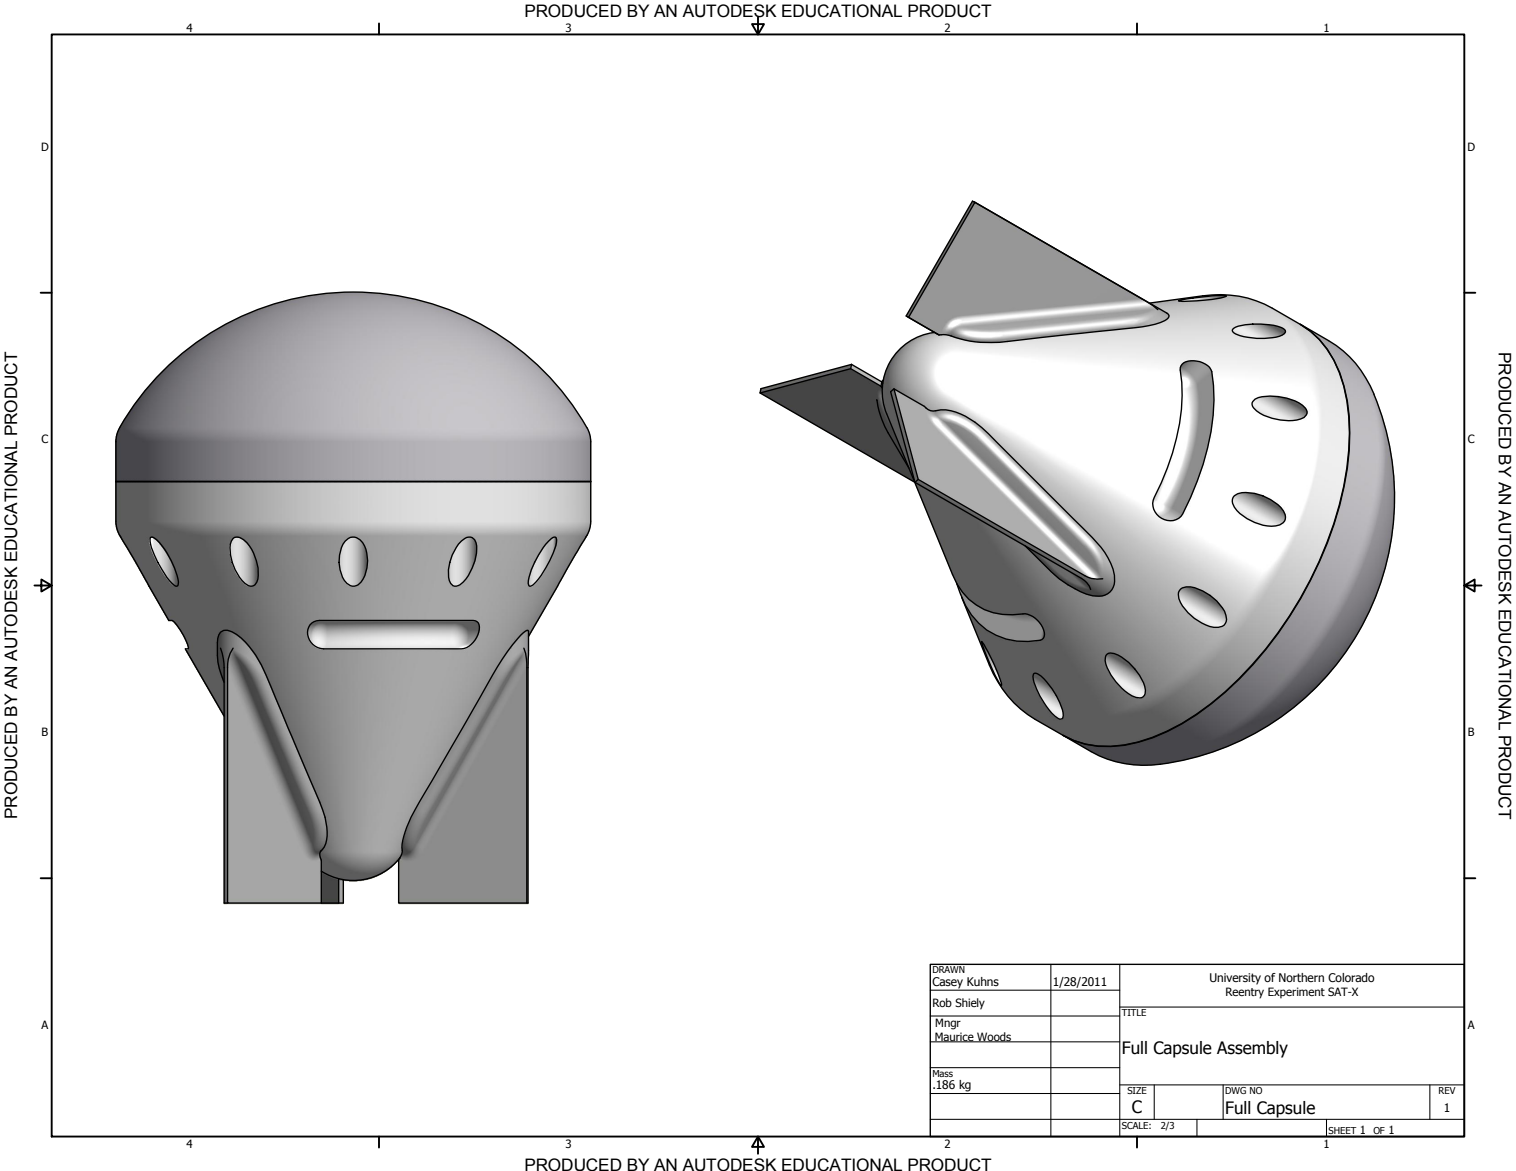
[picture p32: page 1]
TIO N; ull C; ule; bly; olo; ely

PRODUCED BY AN AUTODESK EDUCATIONAL PRODUCT

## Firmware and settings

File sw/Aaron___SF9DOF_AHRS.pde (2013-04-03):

// Sparkfveun 9DOF Razor IMU AHRS
// 9 Degree of Measurement Attitude and Heading Reference System
// Firmware v1.0
//
// Released under Creative Commons License 
// Code by Doug Weibel and Jose Julio
// Based on ArduIMU v1.5 by Jordi Munoz and William Premerlani, Jose Julio and Doug Weibel

// Axis definition: 
   // X axis pointing forward (to the FTDI connector)
   // Y axis pointing to the right 
   // and Z axis pointing down.
// Positive pitch : nose up
// Positive roll : right wing down
// Positive yaw : clockwise

/* Hardware version - v13
	
	ATMega328@3.3V w/ external 8MHz resonator
	High Fuse DA
        Low Fuse FF
	
	ADXL345: Accelerometer
	HMC5843: Magnetometer
	LY530:	Yaw Gyro
	LPR530:	Pitch and Roll Gyro

        Programmer : 3.3v FTDI
        Arduino IDE : Select board  "Arduino Duemilanove w/ATmega328"
*/
// This code works also on ATMega168 Hardware

#include <Wire.h>

// ADXL345 Sensitivity(from datasheet) => 4mg/LSB   1G => 1000mg/4mg = 256 steps
// Tested value : 248
#define GRAVITY 248  //this equivalent to 1G in the raw data coming from the accelerometer 
#define Accel_Scale(x) x*(GRAVITY/9.81)//Scaling the raw data of the accel to actual acceleration in meters for seconds square

#define ToRad(x) (x*0.01745329252)  // *pi/180
#define ToDeg(x) (x*57.2957795131)  // *180/pi

// LPR530 & LY530 Sensitivity (from datasheet) => (3.3mv at 3v)at 3.3v: 3mV/º/s, 3.22mV/ADC step => 0.93
// Tested values : 0.92
#define Gyro_Gain_X 0.92 //X axis Gyro gain
#define Gyro_Gain_Y 0.92 //Y axis Gyro gain
#define Gyro_Gain_Z 0.92 //Z axis Gyro gain
#define Gyro_Scaled_X(x) x*ToRad(Gyro_Gain_X) //Return the scaled ADC raw data of the gyro in radians for second
#define Gyro_Scaled_Y(x) x*ToRad(Gyro_Gain_Y) //Return the scaled ADC raw data of the gyro in radians for second
#define Gyro_Scaled_Z(x) x*ToRad(Gyro_Gain_Z) //Return the scaled ADC raw data of the gyro in radians for second

#define Kp_ROLLPITCH 0.02
#define Ki_ROLLPITCH 0.00002
#define Kp_YAW 1.2
#define Ki_YAW 0.00002

/*For debugging purposes*/
//OUTPUTMODE=1 will print the corrected data, 
//OUTPUTMODE=0 will print uncorrected data of the gyros (with drift)
#define OUTPUTMODE 1

//#define PRINT_DCM 0     //Will print the whole direction cosine matrix
#define PRINT_ANALOGS 1 //Will print the analog raw data
#define PRINT_EULER 0   //Will print the Euler angles Roll, Pitch and Yaw

#define ADC_WARM_CYCLES 50
#define STATUS_LED 13 

int8_t sensors[3] = {1,2,0};  // Map the ADC channels gyro_x, gyro_y, gyro_z
int SENSOR_SIGN[9] = {-1,1,-1,1,1,1,-1,-1,-1};  //Correct directions x,y,z - gyros, accels, magnetormeter

float G_Dt=0.02;    // Integration time (DCM algorithm)  We will run the integration loop at 50Hz if possible

long timer=0;   //general purpuse timer
long timer_old;
long timer24=0; //Second timer used to print values 
int AN[6]; //array that store the 3 ADC filtered data (gyros)
int AN_OFFSET[6]={0,0,0,0,0,0}; //Array that stores the Offset of the sensors
int ACC[3];          //array that store the accelerometers data

int accel_x;
int accel_y;
int accel_z;
int magnetom_x;
int magnetom_y;
int magnetom_z;
float MAG_Heading;

float Accel_Vector[3]= {0,0,0}; //Store the acceleration in a vector
float Gyro_Vector[3]= {0,0,0};//Store the gyros turn rate in a vector
float Omega_Vector[3]= {0,0,0}; //Corrected Gyro_Vector data
float Omega_P[3]= {0,0,0};//Omega Proportional correction
float Omega_I[3]= {0,0,0};//Omega Integrator
float Omega[3]= {0,0,0};

// Euler angles
float roll;
float pitch;
float yaw;

float errorRollPitch[3]= {0,0,0}; 
float errorYaw[3]= {0,0,0};

unsigned int counter=0;
byte gyro_sat=0;

float DCM_Matrix[3][3]= {
  {
    1,0,0  }
  ,{
    0,1,0  }
  ,{
    0,0,1  }
}; 
float Update_Matrix[3][3]={{0,1,2},{3,4,5},{6,7,8}}; //Gyros here


float Temporary_Matrix[3][3]={
  {
    0,0,0  }
  ,{
    0,0,0  }
  ,{
    0,0,0  }
};
 
//ADC variables
volatile uint8_t MuxSel=0;
volatile uint8_t analog_reference;
volatile uint16_t analog_buffer[8];
volatile uint8_t analog_count[8];

void setup()
{ 
  Serial.begin(115200);
  pinMode (STATUS_LED,OUTPUT);  // Status LED
  
  Analog_Reference(DEFAULT); 
  Analog_Init();
  I2C_Init();
  Accel_Init();
  Read_Accel();

  Serial.println("Sparkfun 9DOF Razor AHRS");

  digitalWrite(STATUS_LED,LOW);
  delay(1500);
 
  // Magnetometer initialization
  Compass_Init();
  
  // Initialze ADC readings and buffers
  Read_adc_raw();
  delay(20);
  
  for(int i=0;i<32;i++)    // We take some readings...
    {
    Read_adc_raw();
    Read_Accel();
    for(int y=0; y<6; y++)   // Cumulate values
      AN_OFFSET[y] += AN[y];
    delay(20);
    }
    
  for(int y=0; y<6; y++)
    AN_OFFSET[y] = AN_OFFSET[y]/32;
    
  AN_OFFSET[5]-=GRAVITY*SENSOR_SIGN[5];
  
  //Serial.println("Offset:");
  for(int y=0; y<6; y++)
    Serial.println(AN_OFFSET[y]);
  
  delay(2000);
  digitalWrite(STATUS_LED,HIGH);
    
  Read_adc_raw();     // ADC initialization
  timer=millis();
  delay(20);
  counter=0;
}

void loop() //Main Loop
{
/*  if((millis()-timer)>=1)  // Main loop runs at 50Hz
  {
    counter++;
    timer_old = timer;
    timer=millis();
    if (timer>timer_old)
      G_Dt = (timer-timer_old)/1000.0;    // Real time of loop run. We use this on the DCM algorithm (gyro integration time)
    else
      G_Dt = 0;*/
    
    // *** DCM algorithm
    // Data adquisition
  //Read_adc_raw();   // This read gyro data
  Read_Accel();     // Read I2C accelerometer
    
    //if (counter > 5)  // Read compass data at 10Hz... (5 loop runs)
     // {
      //counter=0;
   //Read_Compass();    // Read I2C magnetometer
   //Compass_Heading(); // Calculate magnetic heading  
     // }
    
    // Calculations...
    //Matrix_update(); 
    //Normalize();
    //Drift_correction();
    //Euler_angles();
    // ***
    
   Serial.print(millis());
   Serial.print(", ");
      Serial.print(ACC[0]);
      Serial.print (",");
      Serial.print(ACC[1]);
      Serial.print (",");
      Serial.print(ACC[2]);
      Serial.println();
 //printdata();
    
    
    //Turn off the LED when you saturate any of the gyros.
   /*if((abs(Gyro_Vector[0])>=ToRad(300))||(abs(Gyro_Vector[1])>=ToRad(300))||(abs(Gyro_Vector[2])>=ToRad(300)))
      {
      if (gyro_sat<50)
        gyro_sat+=10;
      }
    else
      {
      if (gyro_sat>0)
        gyro_sat--;
      }
  
    if (gyro_sat>0)
      digitalWrite(STATUS_LED,LOW);  
    else
      digitalWrite(STATUS_LED,HIGH); */
  
  //}
   
}

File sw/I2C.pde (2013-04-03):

/* ******************************************************* */
/* I2C code for ADXL345 accelerometer                      */
/* and HMC5843 magnetometer                                */
/* ******************************************************* */

int AccelAddress = 0x53;
int CompassAddress = 0x1E;  //0x3C //0x3D;  //(0x42>>1);

void I2C_Init()
{
  Wire.begin();
}

void Accel_Init()
{
  Wire.beginTransmission(AccelAddress);
  Wire.send(0x2D);  // power register
  Wire.send(0x08);  // measurement mode
  Wire.endTransmission();
  delay(5);
  Wire.beginTransmission(AccelAddress);
  Wire.send(0x31);  // Data format register
  Wire.send(0x08);  // set to full resolution
  Wire.endTransmission();
  delay(5);	
  // Because our main loop runs at 50Hz we adjust the output data rate to 50Hz (25Hz bandwidth)
  Wire.beginTransmission(AccelAddress);
  Wire.send(0x2C);  // Rate register
  Wire.send(0x0F);  // set to 50Hz, normal operation (09 = 50Hz, 0F = 3200Hz)
  Wire.endTransmission();
  delay(5);
}

// Reads x,y and z accelerometer registers
void Read_Accel()
{
  int i = 0;
  byte buff[6];
  
  Wire.beginTransmission(AccelAddress); 
  Wire.send(0x32);        //sends address to read from
  Wire.endTransmission(); //end transmission
  
  Wire.beginTransmission(AccelAddress); //start transmission to device
  Wire.requestFrom(AccelAddress, 6);    // request 6 bytes from device
  
  while(Wire.available())   // ((Wire.available())&&(i<6))
  { 
    buff[i] = Wire.receive();  // receive one byte
    i++;
  }
  Wire.endTransmission(); //end transmission
  
  if (i==6)  // All bytes received?
    {
    ACC[1] = (((int)buff[1]) << 8) | buff[0];    // Y axis (internal sensor x axis)
    ACC[0] = (((int)buff[3]) << 8) | buff[2];    // X axis (internal sensor y axis)
    ACC[2] = (((int)buff[5]) << 8) | buff[4];    // Z axis
    AN[3] = ACC[0];
    AN[4] = ACC[1];
    AN[5] = ACC[2];
    accel_x = SENSOR_SIGN[3]*(ACC[0]-AN_OFFSET[3]);
    accel_y = SENSOR_SIGN[4]*(ACC[1]-AN_OFFSET[4]);
    accel_z = SENSOR_SIGN[5]*(ACC[2]-AN_OFFSET[5]);
    }
  else
    Serial.println("!ERR: Acc data");
}

void Compass_Init()
{
  Wire.beginTransmission(CompassAddress);
  Wire.send(0x02); 
  Wire.send(0x00);   // Set continouos mode (default to 10Hz)
  Wire.endTransmission(); //end transmission
}

void Read_Compass()
{
  int i = 0;
  byte buff[6];
 
  Wire.beginTransmission(CompassAddress); 
  Wire.send(0x03);        //sends address to read from
  Wire.endTransmission(); //end transmission
  
  //Wire.beginTransmission(CompassAddress); 
  Wire.requestFrom(CompassAddress, 6);    // request 6 bytes from device
  while(Wire.available())   // ((Wire.available())&&(i<6))
  { 
    buff[i] = Wire.receive();  // receive one byte
    i++;
  }
  Wire.endTransmission(); //end transmission
  
  if (i==6)  // All bytes received?
    {
    // MSB byte first, then LSB, X,Y,Z
    magnetom_x = SENSOR_SIGN[6]*((((int)buff[2]) << 8) | buff[3]);    // X axis (internal sensor y axis)
    magnetom_y = SENSOR_SIGN[7]*((((int)buff[0]) << 8) | buff[1]);    // Y axis (internal sensor x axis)
    magnetom_z = SENSOR_SIGN[8]*((((int)buff[4]) << 8) | buff[5]);    // Z axis
    }
  else
    Serial.println("!ERR: Mag data");
}

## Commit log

2013-04-03 Lots more stuff
    [ProbeCDH_r1.0.brd, ProbeCDH_r1.0.sch, ProbeEPS_r1.0.brd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]
2013-04-03 SO MUCH STUFF!!!!
    [ANSI B18.3.1M - M1.6x0.35 x 3(1).ipt, ANSI B18.3.1M - M2.5x0.45 x 10(1).ipt, ANSI B18.3.1M - M2.5x0.45 x 12(1).ipt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]
